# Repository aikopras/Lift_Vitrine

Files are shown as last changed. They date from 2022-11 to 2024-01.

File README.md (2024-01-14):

## Decoders and software for a model train lift (elevator, fiddle yard) ##

This software allows you to control a model train lift (elevator, fiddle yard). The photo below shows the lift at the right, and the display case (vitrine) at the left; if you click on the photo you'll see the lift in action (YouTube video; you may find there  [additional videos](https://youtube.com/playlist?list=PLT8t59Iv1uii5TKU-r4GmLXoBTifbTNtb)).

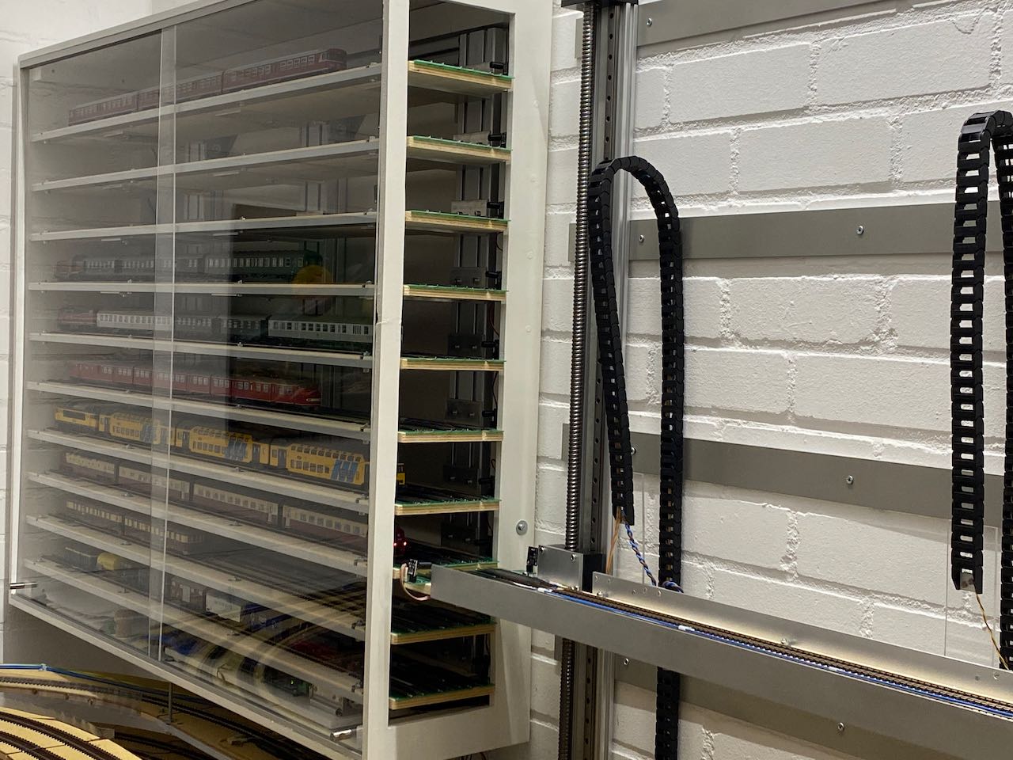
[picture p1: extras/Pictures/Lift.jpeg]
[](https://youtu.be/MswR5I-5q1c?si=-zvIIBghLZpLA2uD)

## Features ##
- Full open source (software as well as hardware).
- Can be used for up to 11 lift levels.
- The lift can be manually operated, using buttons, or by sending DCC accessory (switch) commands.
- [Full automatic operation possible](https://youtu.be/yOJ_Ovc0gCI?si=8jlIXjwKSL-hw6U0), by model train control software such as TrainController.
- Runs on ATMega 2560 processor.
- Two (open source) PCBs are available: a [SMD](https://oshwlab.com/aikopras/support-lift-controller) and a [THT](https://oshwlab.com/aikopras/lift-decoder-arduino-mega-tht) board.
- Provides feedback regarding the current lift position, as well as other status information (lift is moving, status IR-sensors)
- Feedback is provided via the (Lenz) RS-Bus. Interfacing with other feedback systems is possible, however.
- For extra safety: can be combined with IR-Sensors, to avoid lift movement if trains block the passage to/from the lift.
- For extra safety: relays can be connected to switch track power off if the lift is moving.
- Can control one or two stepper motors.
- Relies on GRBL to control the steppers motor, via a dedicated ATMega 328 / Arduino Nano.
- Allows homing, to guarantee exact positioning of the lift.
- For debugging purposes, a serial interface and / or LCD display can be connected.

## Overall structure ##
The system consists of three parts:
- **Main controller**: The main controller interfaces via the GRBL controller to the stepper drivers and motors that move the lift. The Main controller listens to DCC accessory as well as button controller commands that tell the lift to move to a certain position. The Main controller provides feedback information via the RS-Bus and its onboard connectors.
- **Button controller**: The Button controller connects to the buttons that allow manual movement of the lift. Buttons may include LEDs for visual feedback.
- **IR controller**: The IR-Sensor controller connects to the IR-LEDs and sensors that monitor if the passage to/from the lift is occupied by some train, or free.
- **RS-485**: The three controllers are connected to each other via the RS-485 bus.

A minimum system consists of a main controller only; in that case DCC switch commands will move the lift. If the button controller is attached as well, the lift may also be operated via the button interface. Note that, in such case, the lift can also be used without a DCC connection. Protection via the IR-Sensor controller enhances safety, but is optional.

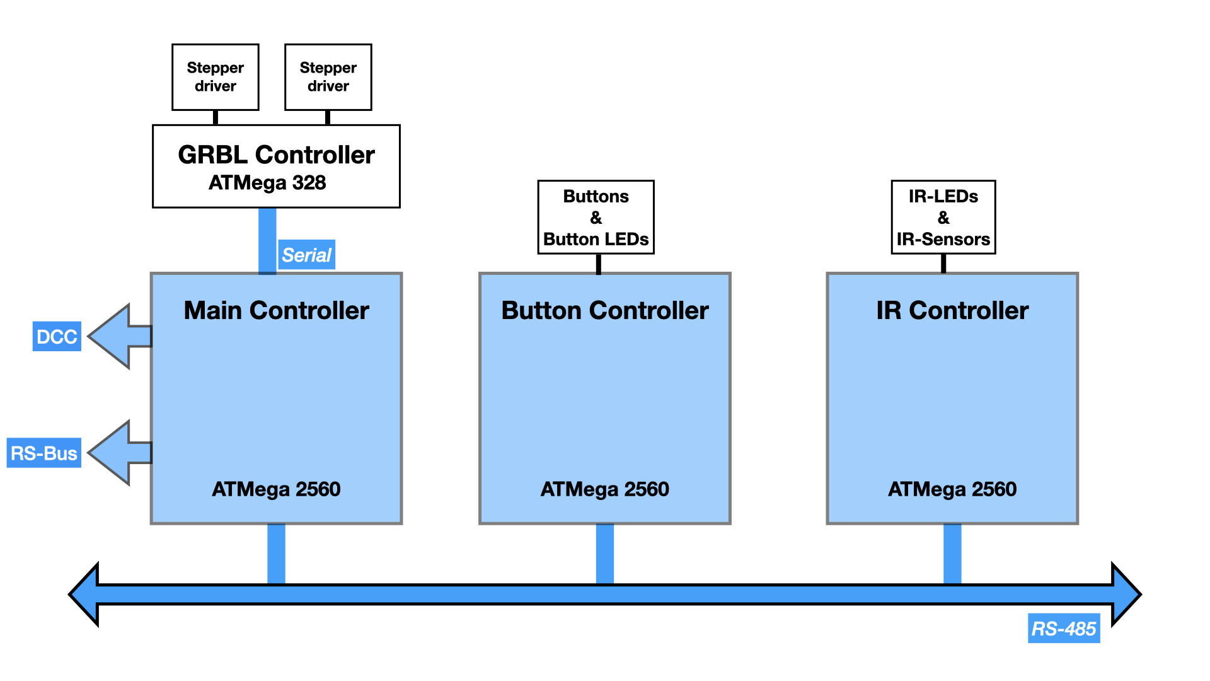
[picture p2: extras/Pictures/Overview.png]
Overview

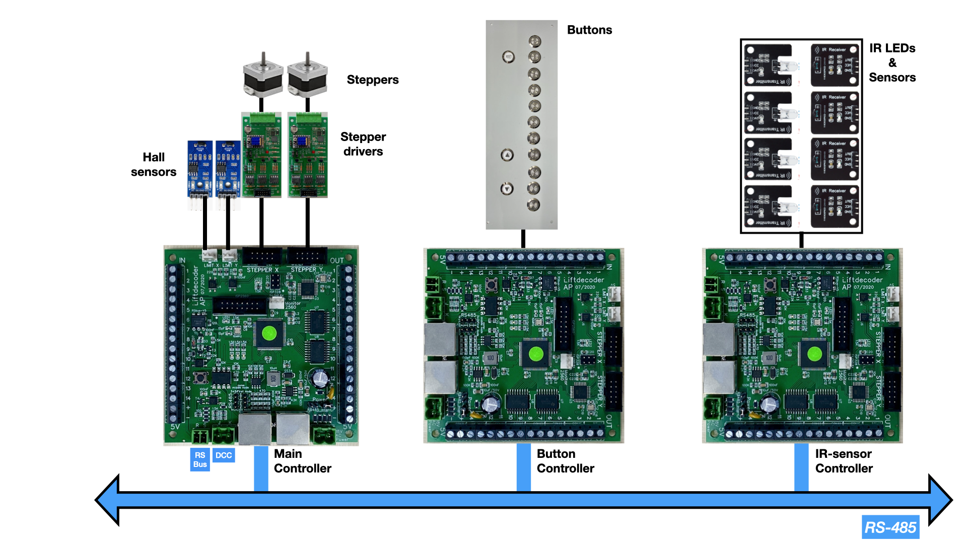
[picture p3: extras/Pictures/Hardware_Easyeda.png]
Hardware-EasyEda


## Hardware ##
Although the software runs on [standard Arduino boards](extras/Board-THT/Manual-Wiring.md), two boards were developed to make building and installation easier. Both boards are available as open source, and may be modified if desired.

#### THT Board ####
Since the software runs on standard Arduino boards, [a board that interconnects](https://oshwlab.com/aikopras/lift-decoder-arduino-mega-tht) the Arduino MEGA and NANO was developed. The board  includes a 5V power and RS485 module, which can both be bought from various (often Chinese) suppliers. The various components are all Through Hole Technology (THT), which are easy to solder. The red PCB at the bottom left side, is the RS-Bus interface, which is also open source board and available in [THT](https://oshwlab.com/aikopras/rs-bus-tht) and [SMD](https://oshwlab.com/aikopras/rs-bus-smd) versions.

The are [detailed instructions](extras/Board-THT/Assembly_Test.md) on how to compile and test software for this board.

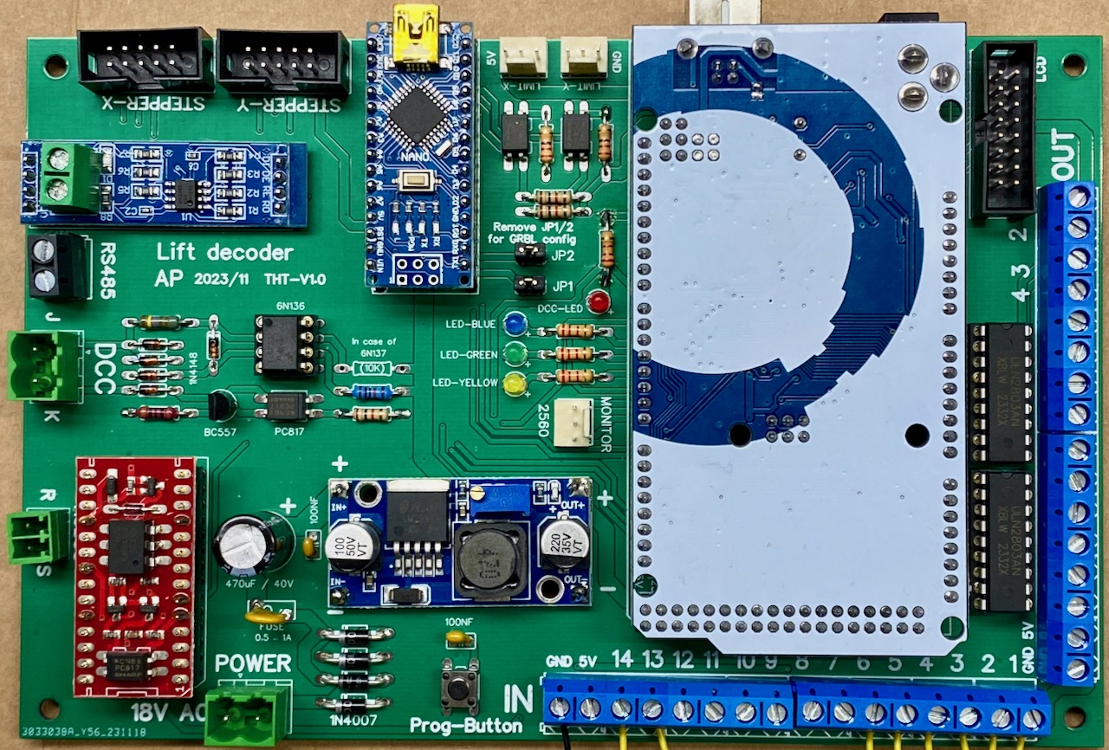
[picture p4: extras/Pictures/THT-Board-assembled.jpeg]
THT Board


#### SMD Board ####
In addition to the THT board, an open source [fully assembled SMD board](https://oshwlab.com/aikopras/support-lift-controller) was developed, that makes building even easier. In fact this board was developed first, after I discovered how cheap it was to order assembled boards in China. For five of these boards I paid in 2019 75 Euro in total. Unfortunately, component prices went up recently and now, January 2024, the costs for these five boards would be something between 125 and 150 Euro. Especially the 2560 processor has become, with 12$, quite expensive.

In September 2023 I noticed that the MP1584 Step-Down Converter is no longer *recommended for new designs*, and should be replaced by another component. That would be relatively simple change, however; on my newer boards I'm already using the TPS54331DR.

An alternative for a future board might be to replace the ATMega 2560 with one of the newer Microchip AVRs, such as an DxCore processor. In my new designs I'm using AVR32DA48 processors, which costs around 2,5$. Unfortunately replacing the chip would require, next to the board, also a redesign of some parts of the software.

The are [detailed instructions](extras/Board-SMD/Assembly_Test.md) on how to compile and test software for this board.

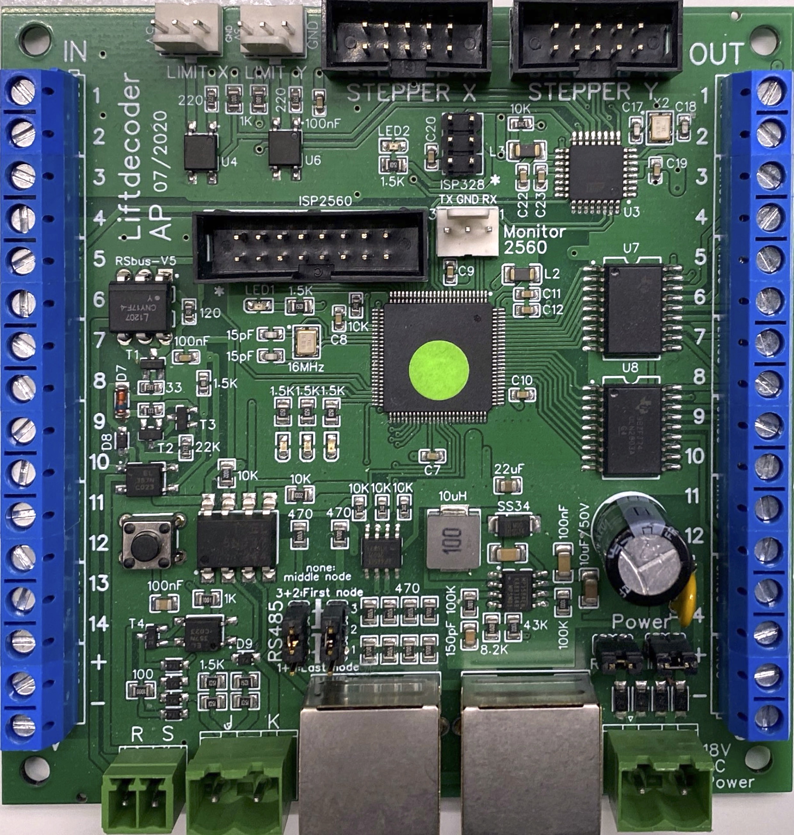
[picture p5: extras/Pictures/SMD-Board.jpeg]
SMD Board


___

## References ##
- [Detailed instructions](extras/Board-THT/Assembly_Test.md) for compiling and testing software for the THT board
- [Detailed instructions](extras/Board-SMD/Assembly_Test.md) for compiling and testing software for the SMD board
- [Loklift controller videos](https://youtube.com/playlist?list=PLT8t59Iv1uii5TKU-r4GmLXoBTifbTNtb)
- [RS485 library for the Loklift decoders](https://github.com/aikopras/AP_RS485_for_Lift_decoders)
- [Discussion of the Loklift on Beneluxspoor forum (Dutch)](https://forum.beneluxspoor.net/index.php?topic=97091.0)
- [Discussion of the Loklift on Stummiforum (German)](https://www.stummiforum.de/t203419f15-Loklift-im-Eigenbau.html)
- [PCB for the THT board](https://oshwlab.com/aikopras/lift-decoder-arduino-mega-tht)
- [PCB for the SMD board](https://oshwlab.com/aikopras/support-lift-controller)
- [PCB for stepper drivers](https://oshwlab.com/aikopras/tmc2209-driver-board)
- [PCB for the DCC/RSbus shield](https://oshwlab.com/aikopras/arduino-uno-dcc-shield)
- [PCB for the RS-Bus (THT)](https://oshwlab.com/aikopras/rs-bus-tht)
- [PCB for the RS-Bus (SMD)](https://oshwlab.com/aikopras/rs-bus-smd)
- [PCB for the RSBus feedback decoders within the vitrine (show case)](https://oshwlab.com/aikopras/vitrine-decoder)
- [PCB to connect/align the three parallel tracks in the vitrine (show case)](https://oshwlab.com/aikopras/tracks-vitrine)

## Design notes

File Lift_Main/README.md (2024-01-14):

# Main Lift Controller #

This is the software for the Main Lift Controller.
The software has been tested on the following lift decoder boards:
  - SMD board: https://oshwlab.com/aikopras/support-lift-controller
  - THT board: https://oshwlab.com/aikopras/lift-decoder-arduino-mega-tht

Instructions for compiling can be found on:
  - SMD board: https://github.com/aikopras/Lift_Vitrine/blob/main/extras/Board-SMD/Compile.md
  - THT board: https://github.com/aikopras/Lift_Vitrine/blob/main/extras/Board-THT/Compile.md

## Modes of operation ##
The Main Lift Controller can be manually and/or automatically operated:
- Manually, via pushing a button that is attached to the button controller.
- Automatically, by sending a DCC Accessory (switch) Command.

### LEDs ###
The LEDs have the following meaning:
- Blue: The blue LED blinks whenever the stepper motors are active.
- Green: The green LED indicates that power is connected and the IR sensors are free (or disabled).
- Yellow: The yellow LED mimics the LEDs on the remote button panel (without flashing).
- Red: The red LED blinks twice during startup, and once whenever a RSbus feedback message is send (see the feedback section below). If no DCC address has been connected yet, the red LED blinks continuously.

### Buttons ###
If the lift is not moving, the following button behavior is possible:
 - Short press of one of the level (0..11) buttons: Lift starts moving to the requested level.
 - Short press of the RESET button: a homing cycle will be initiated.
 - Press of ^ or v buttons: Lift moves in small steps up or down (jogging).
 - Long press of one of the level buttons: the current position will be stored as new the position for that level

While the lift moves, the associated button LED will slowly flash.
Once the move is complete, the button LED will shortly light and subsequently dim. If a new position is being stored, the button LED will flash quickly.

If the lift is moving, all buttons are ignored, except the RESET button. If the RESET button is pushed (short press), the lift will immediately be stopped (see emergence stop below).

### DCC address ###
The common approach for all my DCC decoder boards, is to compile the DCC address with an "illegal" value. This triggers the board to notify the user, via blinking of the red LED, that a DCC address needs to be entered. Like all other decoder boards, this DCC address can be set using the onboard programming button. This new address is permanently stored (in EEPROM), and the next time the decoder starts, the valid DCC address is read from EEPROM and the red LED no longer blinks.

However, you might prefer to set the DCC address already at compile time. This can be done by changing the CV1 and CV9 settings in the file [mySettings.h](mySettings.h)

### RS-Bus address ###
The onboard programming button is not only used to set the DCC address, but indirectly also the RS-Bus address. If you select a decoder address < 128 (thus a switch addresses <509), the RS-Bus address becomes equal to the decoder address (+1). If you select a decoder address >=128, the RS-Bus address becomes 0, meaning "not used". Via the onboard programming button it is therefore not possible to use decoder addresses >=128, in combination with RS-Bus feedback.

Fortunately, we can still use DCC decoder addresses >=128, in combination with RS-Bus feedback, provided we select the RSBus addresses, before compilation, in the file [mySettings.h](mySettings.h).

### Feedback ###
Feedback is provided regarding the lift's position and status. There are twelve level and three status bits. During movement of the lift, all feedback bits are cleared. The three status bits indicate if:
- the IR-sensors are free (provided IR-sensors are active)
- the Lift has arrived / is at level x. There is no movement and the stepper motors are idle
- the lift is ready.<BR>
If the IR-Sensors are active, this bit is the same as 'IR-sensors are free' AND 'Lift is at level x'.<BR>
If the IR-Sensors are inactive, this bit is the same as 'Lift is at level x'.
Analyzing this single bit may, in TrainControl (or whatever software you have), be easier than analyzing two bits.

Feedback is provided in two ways.
1. Using the RS-Bus. We use two addresses; the meaning of the individual bits, is as follows:
 - Base address    : Level 0..7                (low and high nibble. Bit 0..7)
 - Base address + 1: Level 8..11               (low nibble.          Bit 0..3)
 - Base address + 1: IR-sensors are free       (high nibble          Bit 4)
 - Base address + 1: Lift is at level x        (high nibble          Bit 5)
 - Base address + 1: Lift Ready                (high nibble          Bit 7)
2. Using the connectors on the Main Lift Board connectors (added in V2.0).<BR>
Its purpose is to facilitate the use of alternative feedback systems. Although not tested, it is expected to work with other feedback interfaces, such as the LDT RM-88-N-O, the YaMoRC YD6016LN-OPTO and YD6016ES-OPTO, Uhlenbrock 63330 etc.

  - The connectors labelled "IN 1..12" are used to tell which level the lift currently is.
  The connector labelled "1" is for level "0", etc.
  - The connector labelled "IN 13" is used to tell that IR-sensors are free.
  - The connector labelled "IN 14" is used to tell that lift has arrived / is  at level x.
  - The pin labelled "OUT 1" is to tell that the lift is ready.

Note that the IN connectors are directly connected to pins on the ATMega 2560 processor, (accidental) shortcut of these pins will destroy the processor.
Therefore ensure you always use resistors with a value of 1 kOhm or higher.

### Emergency stop ###
If the lift is moving, it can be stopped by either pushing the RESET button, or by sending a DCC Emergency Stop command (= Broadcast ResetCmd). In both cases the RESET button will quickly flash.
1. BUTTON: The Button generates a soft_reset, which immediately halts the steppers and resets GRBL. If reset while in motion, GRBL will throw an Alarm to indicate position may be lost from the motion halt. The Alarm state is signaled via the RESET Button LED, which quickly flashes. A second push of the RESET button is needed to leave the Alarm state. The lift stays at an  undefined position.
2. DCC Emergency Stop command: generates a GRBL feedhold, This allows to lift to continue its movement afterwards. In case the lift should not restart its movement after the DCC emergency stop, while still in the HOLD state, the reset-button which will trigger a soft-reset.

# Initialization #
Before the Main Lift Controller can be used, a number of settings must first be made in the file [mySettings.h](mySettings.h).

##### 1) Tell the sketch which board will be used #####
As mentioned at the top of this page, the lift controller code has been tested on a SMD and a THT board. Although the decoder software will also run on other boards, it is important that the processor is an ATMega 2560 and that the correct connections are made between the processor pins and the various peripherals. Some of these assignments are made in the file [hardware.h](hardware.h) (the DCC, RSBus and RS485 assignments are made by their respective libraries). As can be seen in that file, some small differences exists between the pin assignments for both boards. The reason behind these differences, is that the SMD board  was developed first, and some pins were used that are not available on standard Arduino MEGA boards. Later the THT board was developed, which made some pin changes necessary. The choice between both boards is made via a `#define`.

To use the SMD board, enable the associated `#define`.
```
    #define BOARD_SMD
```
For the THT board, enable the other `#define`:
```
    #define BOARD_THT
```
##### 2) Homing #####
By default, a homing cycle for the stepper motor(s) is performed at program start. Such homing cycle ensures that the lift will move to a defined position. Uncomment the `#define` (remove the starting //) if homing is NOT desired.
```
    #define NO_HOMING
```

##### 3) IR-Sensors #####
By default, every time before the lift starts moving, the IR-sensors connected to the dedicated IR-Sensor Board will be checked. If a train blocks an IR-beam, the lift will not move. Uncomment the `#define` if the IR-sensors should not be checked. This may be required for testing purposes, or if no IR_Sensor board is connected and needed.
```
    #define NO_IR_SENSORS
```

##### 4) LCD Display #####
By default, the LCD is disabled, to avoid interference with RS-bus feedback and other time critical functions. Such interference is caused by the fact that writing to the LCD screen takes quite some time. For testing purposes, or in cases where time critical functions like RS-bus feedback are not needed, the LCD display may be enabled.
```
    #define ENABLE_LCD
```

##### 5) SERIAL_MONITOR #####
By default, the serial monitor interface is switched off (value = 0).
For entering GRBL commands or debugging, it may be convenient to enable the serial monitor.<BR>
If the value = 1, input from the serial line will be copied to the GRBL processor, and information gets displayed regarding the current lift position.<BR>
If the value = 2, input from the serial line will be copied to the GRBL processor, and all data coming back from the GRBL processor gets displayed.
```
    #define SERIAL_MONITOR 1
```

##### 6) DCC Address #####
The decoder can listen to DCC accessory commands to move the lift to a certain level. Each lift level has its own switch address; the first switch address is for level 0; the second switch address is for level 1, the third for level 2, etc.<BR>
Per 4 switch addresses we need one decoder address. Since the maximum number of lift levels is 12, we listen to three decoder addresses.

The first decoder address is stored in CV1 plus CV9. The relationship between CV1, CV9  and the decoder address is explained in RCN-213 (Section 2.1) and RCN-225.
- the valid range for CV1 is 1..63 (if CV9 == 0) or 0..63 (if CV9 !=0)
- the valid range for CV9 is 0..3  (or 128, if the decoder has not been initialized).

If you don't `#define` these CVs here, the default value for CV1 (myAddrL) = 1 and for CV9 (myAddrH) = 128 (0x80). A CV9 value of 128 indicates that the address has not been set by the user yet (by pushing the button).
In that case the decoder's red LED starts blinking.

If your lift will not  be controlled by DCC, but only manually by buttons, you should change CV9 to 0.

Uncomment both `#defines` below and fill-in the address CVs yourself
```
    #define CV1 56
    #define CV9 3
```

##### 7) Set the RS-Bus addresses #####
The RS-Bus address is stored in CV10 (myRSAddr). Valid addresses are between 1..128. The default value is 0, meaning that the RSbus becomes inactive.
The RS-Bus address 128 is used by all my decoders for PoM feedback.
We need two RS-Bus addresses for all feedback information; only the first address needs to be entered below. This address should therefore be between 1..126.
```
    #define RS_ADDRESS 126
```

#### 8) Relays ####
The decoder board allows the connection of two (bi-stable) relays. These relays can, for example, be used to:
1. ensure that the track that connects the lift to the remaining tracks, will only be powered whenever the lift is at level 0. This would be an additional safety measure
2. allow a change of boosters, depending if the lift is at level 0 or at another level. This avoids potential problems at the border between two booster sections

In case the lift is IDLE and at level 0, both relays will be switched to "position 1". In all other cases both relays will be switched to "position 2".

You may change the pins for external relays, provided they stay somewhere on the OUT 9..14 pins (Port K). If you don't use any relays, just keep the values below.
```
    #define RELAY1_POS1    63  // PIN_PK1 - Number on PCB: OUT 10
    #define RELAY1_POS2    64  // PIN_PK2 - Number on PCB: OUT 11
    #define RELAY2_POS1    65  // PIN_PK3 - Number on PCB: OUT 12
    #define RELAY2_POS2    66  // PIN_PK4 - Number on PCB: OUT 13
```

*Note:* The Lift-decoder outputs become, once activated, low. The load should therefore be connected between the output and +5V. Once activated, the differential voltage becomes something like 4 Volt. This might be enough for a 5 (or 3,3V) relay, but certainly not for a 12V relay. Therefore the connection towards 12V relays should be performed via optocouplers, which "translate" between the 5V output domain, and a separate 12V domain for the relays.   

#### 9) Initial lift positions ####
Initial lift positions. Will be entered into EEPROM if and only if the EEPROM has not been initialized. Once the EEPROM is initialized, values will not be written to EEPROM again, even if you make changes in [mySettings.h](mySettings.h). Later changes regarding lift positions should be made via the buttons.

In case you don't have buttons (since the lift is operated via DCC only), you can enable FORCE_EEPROM_WRITE (see below).
After these values are stored in EEPROM, do NOT modify the values again!! Values are in millimeter (point as decimal separator).
```
    #define LEVEL00       "0.000"
    #define LEVEL01     "100.000"
    #define LEVEL02     "200.000"
    #define LEVEL03     "300.000"
    #define LEVEL04     "400.000"
    #define LEVEL05     "500.000"
    #define LEVEL06     "600.000"
    #define LEVEL07     "700.000"
    #define LEVEL08     "800.000"
    #define LEVEL09     "900.000"
    #define LEVEL10    "1000.000"
    #define LEVEL11    "1100.000"
```

#### 10) Force EEPROM write ####
Set the `#define` below to `1`, if the new values MUST be written to EEPROM. Don't forget to change it back to `0` once the new settings are stored in EEPROM, to avoid EEPROM wear-out.
```
    #define FORCE_EEPROM_WRITE 0
```

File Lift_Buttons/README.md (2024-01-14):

# Buttons controller #

This is the software for the Buttons controller.
The software has been tested on the following lift decoder boards:
  - SMD board: https://oshwlab.com/aikopras/support-lift-controller
  - THT board: https://oshwlab.com/aikopras/lift-decoder-arduino-mega-tht

Instructions for compiling can be found on:
  - SMD board: https://github.com/aikopras/Lift_Vitrine/blob/main/extras/Board-SMD/Compile.md
  - THT board: https://github.com/aikopras/Lift_Vitrine/blob/main/extras/Board-THT/Compile.md

### LEDs ###
**Blue LED:** The blue LED blinks whenever a RS485 request message is received from the main Lift decoder. The main Lift controller polls the Buttons controller every 100ms if a button is pushed. In normal operation the blue LED should therefore blink 10 times per second.

**Green LED:** The green LED indicates the board is powered and the sketch is started.

**Yellow LED:** The yellow LED is set immediately after a button is pushed. It stays on, until an explicit command is received from the Main Lift Controller, saying that the action associated with the button is completed.

**Red LED:** The red LED is not used by the Buttons Controller software.

### Wiring ###
The board has 14 inputs (`IN 1..14`) and 14 outputs (`OUT 1..14`). The outputs are used for the LEDs that are build into each and every button.
The buttons for the various levels should be wired to the `IN 1..11`pins; the Reset button to `IN 12`, and the UP and DOWN buttons to `IN 12` resp. `IN 13`. The other side of the buttons should be connected to `GND`. The LEDs, however, should be connected between the `OUT` pins and` +5V`.

In case you want to make changes, the meaning of the various pins is not defined in the button controller sketch, but in  [rs485.h](../Lift_Main/rs485.h) of the main controller sketch.
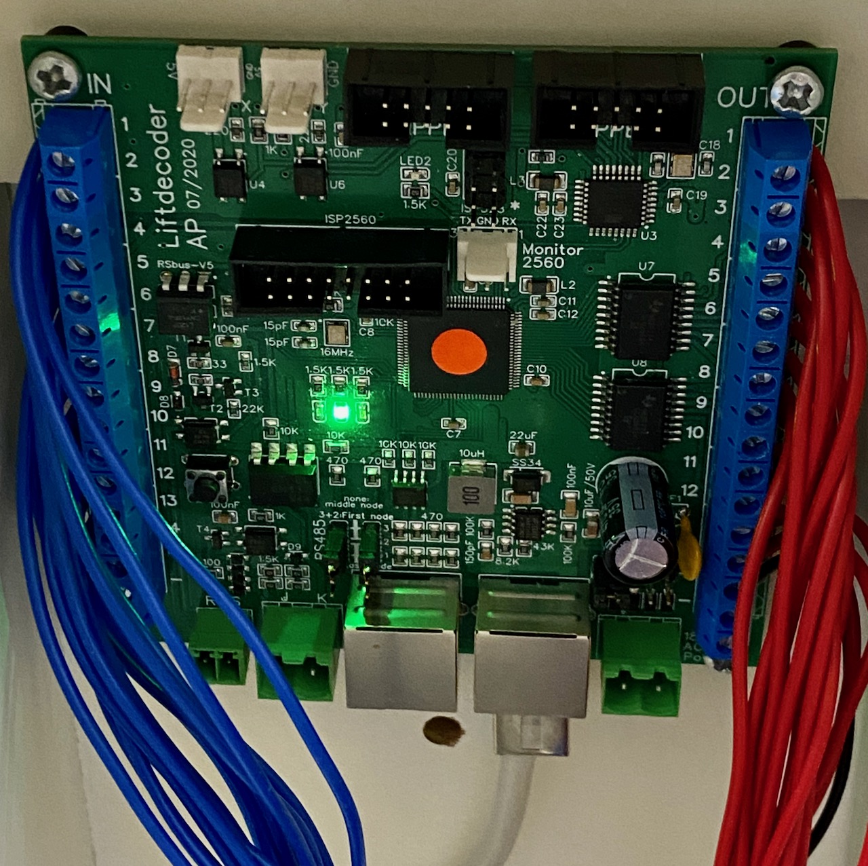
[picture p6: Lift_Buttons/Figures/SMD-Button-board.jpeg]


## Initialization ##
Before the Buttons-controller can be used, the following setting must be made first in the file [mySettings.h](mySettings.h).

##### 1) Tell the sketch which board will be used #####
As mentioned at the top of this page, the lift controller code has been tested on a SMD and a THT board. Although the decoder software will also run on other boards, it is important that the processor is an ATMega 2560 and that the correct connections are made between the processor pins and the various peripherals. Some of these assignments are made in the file [hardware.h](hardware.h) (the DCC, RSBus and RS485 assignments are made by their respective libraries). As can be seen in that file, some small differences exists between the pin assignments for both boards. The reason behind these differences, is that the SMD board  was developed first, and some pins were used that are not available on standard Arduino MEGA boards. Later the THT board was developed, which made some pin changes necessary. The choice between both boards is made via a `#define`.

To use the SMD board, enable the associated `#define`.
```
    #define BOARD_SMD
```
For the THT board, enable the other `#define`:
```
    #define BOARD_THT
```

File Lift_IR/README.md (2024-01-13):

# IR-sensor controller #

This is the software for the Infra-Red (IR) sensor controller.
The software has been tested on the following lift decoder boards:
  - SMD board: https://oshwlab.com/aikopras/support-lift-controller
  - THT board: https://oshwlab.com/aikopras/lift-decoder-arduino-mega-tht

Instructions for compiling can be found on:
  - SMD board: https://github.com/aikopras/Lift_Vitrine/blob/main/extras/Board-SMD/Compile.md
  - THT board: https://github.com/aikopras/Lift_Vitrine/blob/main/extras/Board-THT/Compile.md

### LEDs ###
**Blue LED:** The blue LED blinks whenever a RS485 request message is received from the main Lift decoder. The main Lift controller polls the IR-controller every 100ms for the status of all IR sensors. In normal operation the blue LED should therefore blink 10 times per second.

**Green LED:** The green LED is on, as long as all IR-Sensors are free. At the moment a train blocks an IR-beam, the LED turns off. The IR-sensors are checked 10 times per second, thus changes will be detected within 100ms.

**Yellow LED:** In normal operations the yellow LED will be off. However, by pushing the onboard button, the decoder may be put in debugging mode (see below).

**Red LED:** The red LED blinks twice during startup, and once whenever a RSbus feedback message is send. Such feedback messages are send whenever a change in the status of one or more sensors is detected.

### Debugging mode ###
Debugging mode is entered, whenever the onboard button is pushed. If the button is pushed again, debugging mode will be turned off. The yellow LED indicates whether debugging mode is on or off.

In debugging mode, status information of every individual sensor is send over the Serial Interface and can thus be examined using the Arduino's Serial Monitor. Baudrate should be 115200 baud.

Sending data over the Serial Line is relatively CPU intensive and may sometimes interfere with normal operations. Therefore debugging mode should be off, unless you really need to check for errors.
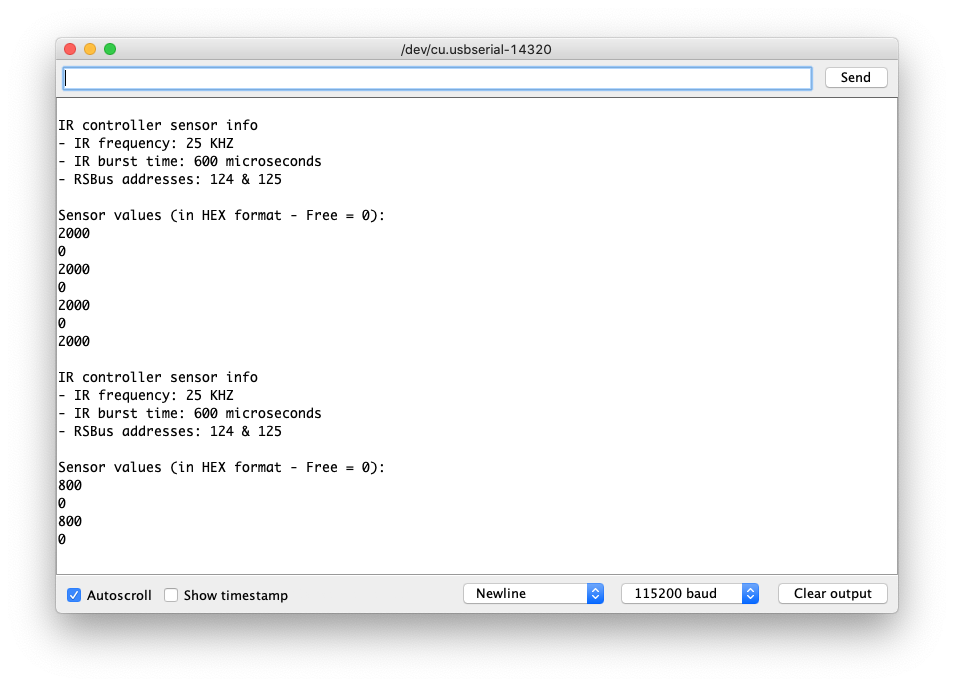
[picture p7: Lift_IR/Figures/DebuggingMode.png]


## Sensors ##
For my lift, I've used the following IR-LEDs and Sensors. They are quite inexpensive and can be obtained from sources such as Ali. A problem with these LEDs, is that light goes into many directions, potentially leading to reflections. Due to reflections, the sensor (receiver) may still receive IR-light, despite the fact that the direct beam is blocked by a train. Therefore, to focus the IR-beam a bit, a black tube has been put around the sides of the LED.

##### Connections: #####
  - Receiver: GND goes to the decoder's GND (-), VCC goes to the decoder's 5V; DAT goes to one of the 14 decoder's input pins.
  - IR-LED: S (pin left) goes via a resistor of 1 Kohm or higher to the decoder's 5V; - (pin right) goes to the corresponding decoder's output pin; the pin in the middle will not be connected. Note that the LED *must* be connected (via a resistor) between the output pin and ***+5V***, and not to the decoder's *GND (-)*. This is because the decoder uses ULN 2803 output drivers, which are either Low or Undefined.

<table><tr>
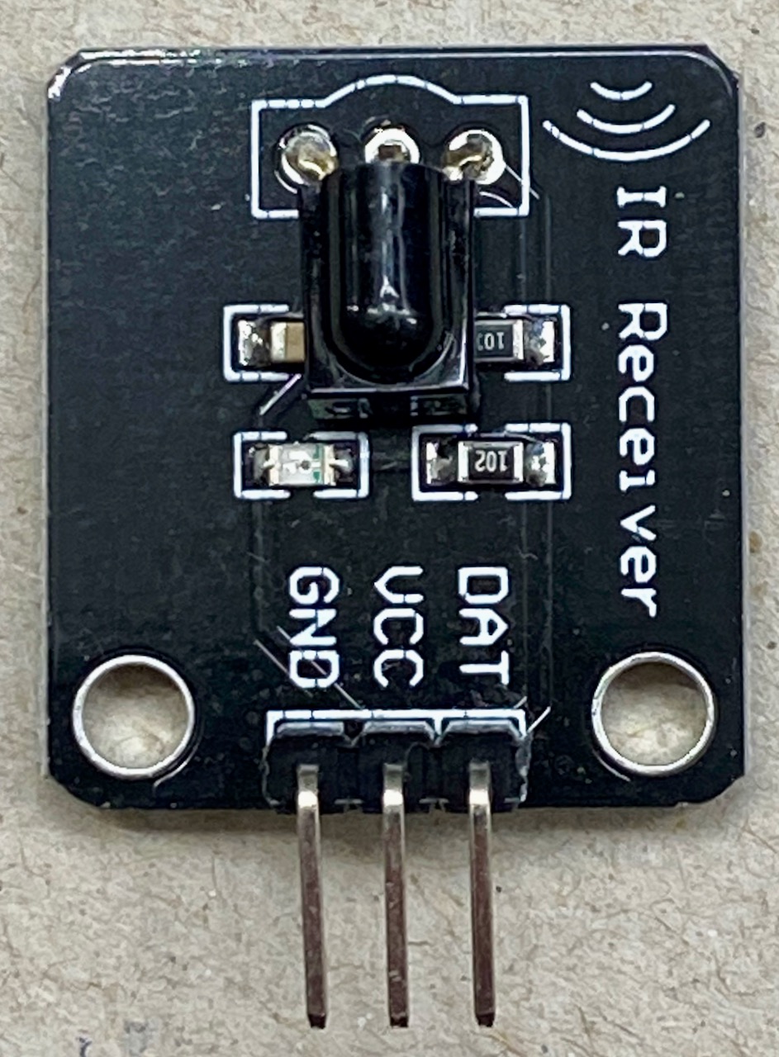
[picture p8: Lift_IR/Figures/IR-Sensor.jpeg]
Sensor
<td>  </td>
<td> <img src="Figures/IR-LED2.jpeg" alt="IR-LED2" "/> </td>
</tr></table>

## Initialization ##
Before the IR-controller can be used, a number of settings must be made first in the file [mySettings.h](mySettings.h).

##### 1) Tell the sketch which board will be used #####
As mentioned at the top of this page, the lift controller code has been tested on a SMD and a THT board. Although the decoder software will also run on other boards, it is important that the processor is an ATMega 2560 and that the correct connections are made between the processor pins and the various peripherals. Some of these assignments are made in the file [hardware.h](hardware.h) (the DCC, RSBus and RS485 assignments are made by their respective libraries). As can be seen in that file, some small differences exists between the pin assignments for both boards. The reason behind these differences, is that the SMD board  was developed first, and some pins were used that are not available on standard Arduino MEGA boards. Later the THT board was developed, which made some pin changes necessary. The choice between both boards is made via a `#define`.

To use the SMD board, enable the associated `#define`.
```
    #define BOARD_SMD
```
For the THT board, enable the other `#define`:
```
    #define BOARD_THT
```
##### 2) Tell the sketch which I/O ports are used for the sensors #####
The lift decoder boards have 14 general purpose in- and outputs. Therefore a maximum of 14 sensors (IR-LEDs and IR-Receivers) may be connected (the software would facilitate 16). To tell the software which inputs/outputs are wired, a bitmask `MASK_SENSORS_CONNECTED` is used. The lowest order (rightmost) bit in that mask corresponds to the IN/OUT pair of the blue connectors that are labelled 1. Below are some examples:
 - `0b0000000000000001` a single sensor is connected to IN/OUT 1
 - `0b0000000000000011` two sensors are connected to IN/OUT 1 and 2
 - `0b0000000000000010` a single sensor is connected to IN/OUT 2
 - `0b0000111111111111` twelve sensors are connected to IN/OUT 1..12
 - `0b0011111111111111` all 14 sensors are connected

Again a `#define` is used to set the bit mask. Below the default setting for twelve sensors connected to IN/OUT 1..12:
```
    #define MASK_SENSORS_CONNECTED 0b0000111111111111
```

##### 3) Set the sensor sensitivity #####
The sensitivity of the IR LEDs and receivers is best around 38kHz. Unfortunately, at 38kHz the system may become too sensitive, allowing reflections to generate false negatives. A false negative occurs whenever a train blocks the direct IR-beam between LED and receiver, but because of reflections the receiver still receives IR-signals and therefore fails to detect the train.

There are several means to limit the effect of reflections. First, the software checks a single LED-receiver pair at a time; the receiver therefore never receives a beam coming from a different LED. Second, a small tube around the LED (see photo above) will focus the beam into a smaller beam. Third, the resistor in series with the LED limits the current flowing through the LED, and thus the strength of the IR-beam. In my layout I've used resistors with a value of 1 kOhm, but in hindsight a higher value would have been a better choice.

Fortunately there are also other ways to limit sensitivity. IR-LEDs and receivers usually operate at 38kHz, but will also operate at lower (or higher) frequencies, although less sensitive. To decrease the sensitivity of the sensors, we can therefore lower the frequency to, for example, a value of 25kHz. Depending on your specific situation, you may have to experiment with this value to find the value that works best. Again we will use a `#define` for that.

Next to modifying the KHZ value, we may also play with the time the burst lasts. To avoid the receiver from saturation, the burst of IR pulses may not become too long. In practice, a reasonable value will be something between 15 to 30 pulses, which corresponds (roughly) to anything between 375 us (15 x 25) and 750 us.

Below are the default values for 25 kHz and 600 us burst time:
```
#define KHZ 25                       // Frequency at which we operate the IR system
#define BURST_TIME 600               // Time in us the burst will last
```

##### 4) Set the RS-Bus addresses #####
Although the Main Lift Controller board signals to the DCC system / control computer whether all IR-Sensors are free or not (using a single bit), it may sometimes be convenient to also know the status of each individual sensor. This is particularly true in case of possible errors.  To facilitate individual sensor feedback, we use the RS feedback bus. We need two RSBus addresses for that, to accommodate a maximum of 16 sensors (although the board supports "only" 14 sensors).

You may change the addresses to any value you like. In case you don't use RSBus feedback, you should still have the addresses configured, to avoid compile errors. Below are the default values (note that this time we do not use a `#define`, but `const uint8_t`):
```
const uint8_t RS_AddresLow = 124;     // 1.. 128
const uint8_t RS_AddresHigh = 125;    // 1.. 128
```

##### 5) Speed versus portability #####
To increase speed, we can use for the IR-beam generation two of the three General Purpose I/O Registers (GPIORs) that are available on a ATMega 2560.
```
    #define PORT GPIOR0                   // Fast, but may interfere with other libraries
    #define BITMASK GPIOR1                 
```
To use these GPIORs, we have to be certain however that they are not yet used elsewhere in the software. The AP-DCC-Library, for example, already uses GPIOR0 and GPIOR1. In cases where we know that we can't use these GPIORs, or in cases where we obtain strange errors, we can use `volatile uint8_t` variables instead. This makes the code run less efficient, but improves portability.

```
    volatile uint8_t PORT;              // Slow, but more portable
    volatile uint8_t BITMASK;
```

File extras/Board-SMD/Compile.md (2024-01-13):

## MegaCore - Compile and upload ##

To compile and upload a lift-decoder sketch, select the MegaCore board, the ATmega 2560 processor, MEGA pinout, and "no bootloader". For other settings see below. Select the programmer you have. <BR>
Upload the sketch (**Upload** button or **Sketch => Using Programmer**).
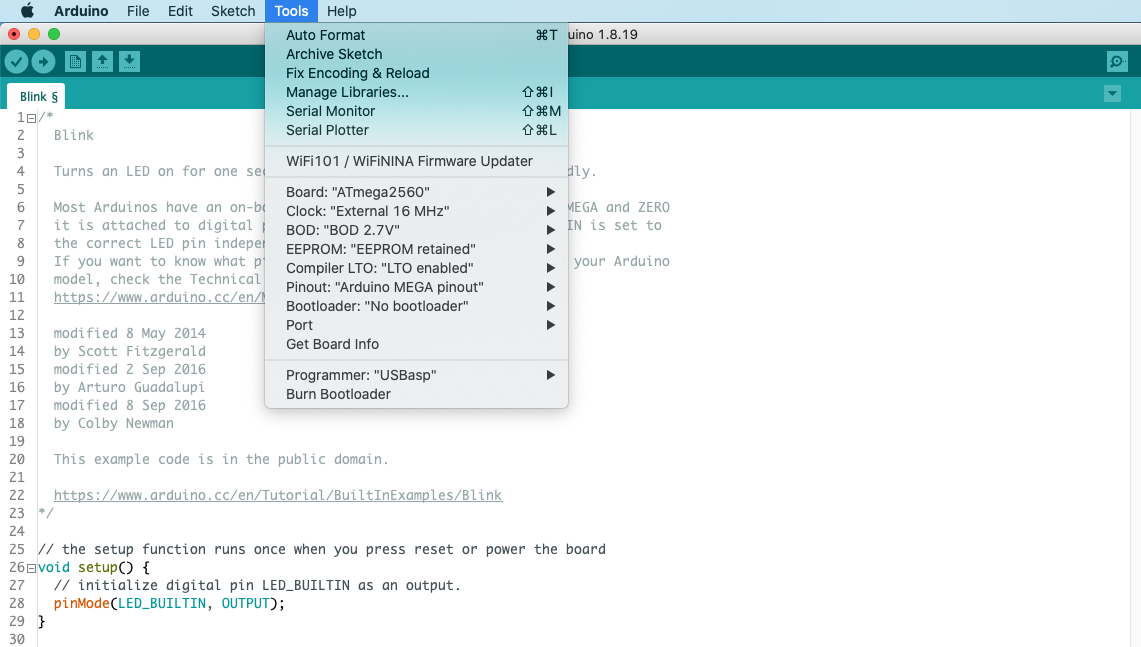
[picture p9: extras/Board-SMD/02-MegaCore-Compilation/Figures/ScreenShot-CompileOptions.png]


### MegaCore ###
If the Fuses have not yet been set or the MegaCore board  installed, see the instructions [here](./02-MegaCore-Compilation/Step02-MegaCore-Compilation.md)

### EEPROM retained? ###
The **Tools** menu includes an option called **EEPROM retained**. The idea behind this option is that, during compilation, a choice can be made whether the EEPROM should keep its current values, or be cleared / overwritten. Unfortunately, clearing / overwriting seems to be quite unreliable, and depend on several factors, including if / which bootloader is used. In practice the EEPROM will most likely *NOT* be cleared / overwritten.

The Lift decoder boards (and any board that uses the AP_DCC_Decoder_Core library) therefore check, at startup, if the EEPROM is empty (that happens if you use a new board). If that is the case, the EEPROM will be automatically filled with default values (from the [AP_DCC_Decoder_Core](https://github.com/aikopras/AP_DCC_Decoder_Core/blob/main/src/CvValues/CvValues.cpp) library).

In the setup() part of your sketch you may [override](https://github.com/aikopras/AP_DCC_Decoder_Core/blob/main/src/CvValues/CvValues.md) these initial CV values. To store these new CV values in EEPROM, you have to push the onboard button for 5 seconds (or use a PoM message and write to CV8).

The main lift decoder has, in the mySettings.h file, a compiler directive called FORCE_EEPROM_WRITE that will overwrite the EEPROM with new values. This directive can be used instead of the **EEPROM** retained" option in the **Tools** menu.

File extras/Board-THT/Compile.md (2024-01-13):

## MegaCore - Compile and upload ##

To compile and upload a lift-decoder sketch, select the MegaCore board, the ATmega 2560 processor and as Programmer the "Legacy Arduino MEGA bootloader". See below for the other settings. <BR>
Upload the sketch (**Upload** button).
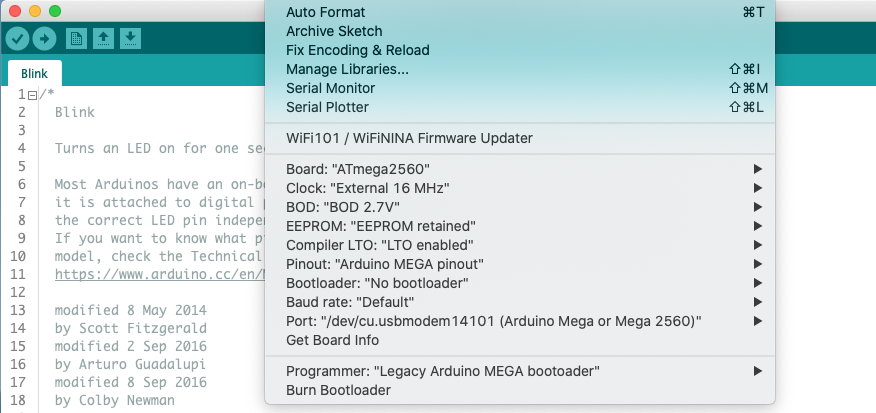
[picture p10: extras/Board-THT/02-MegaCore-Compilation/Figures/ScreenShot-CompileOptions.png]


### MegaCore ###
If the MegaCore board has not yet been installed, see the instructions [here](./02-MegaCore-Compilation/Step02-MegaCore-Compilation.md)

### EEPROM retained? ###
The **Tools** menu includes an option called **EEPROM retained**. The idea behind this option is that, during compilation, a choice can be made whether the EEPROM should keep its current values, or be cleared / overwritten. Unfortunately, clearing / overwriting seems to be quite unreliable, and depend on several factors, including if / which bootloader is used. In practice the EEPROM will most likely *NOT* be cleared / overwritten.

The Lift decoder boards (and any board that uses the AP_DCC_Decoder_Core library) therefore check, at startup, if the EEPROM is empty (that happens if you use a new board). If that is the case, the EEPROM will be automatically filled with default values (from the [AP_DCC_Decoder_Core](https://github.com/aikopras/AP_DCC_Decoder_Core/blob/main/src/CvValues/CvValues.cpp) library).

In the setup() part of your sketch you may [override](https://github.com/aikopras/AP_DCC_Decoder_Core/blob/main/src/CvValues/CvValues.md) these initial CV values. To store these new CV values in EEPROM, you have to push the onboard button for 5 seconds (or use a PoM message and write to CV8).

The main lift decoder has, in the mySettings.h file, a compiler directive called FORCE_EEPROM_WRITE that will overwrite the EEPROM with new values. This directive can be used instead of the **EEPROM** retained" option in the **Tools** menu.

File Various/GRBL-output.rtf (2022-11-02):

Below some GRBL input (in red) and the corresponding output.
A detailed description is provided at: https://github.com/gnea/grbl/wiki/Grbl-v1.1-Interface

?
<Idle|MPos:0.000,0.000,0.000|FS:0,0|Ov:100,100,100>
ok

X100
ok
?
<Run|MPos:88.028,0.000,0.000|FS:903,0>
ok
?
<Idle|MPos:100.000,0.000,0.000|FS:0,0>
ok

G90 X300
ok
?
<Run|MPos:283.913,0.000,0.000|FS:1047,0>
ok
?
<Idle|MPos:300.000,0.000,0.000|FS:0,0>
ok

XYZA
error:2

$H (maar zonder switches)
ALARM:8
ok

Grbl 1.1h ['$' for help]
[MSG:'$H'|'$X' to unlock]

$X
[MSG:Caution: Unlocked]
ok

? (Na een mislukte Homing cyclus)
<Idle|MPos:7.700,7.700,0.000|FS:0,0|WCO:0.000,0.000,0.000>
ok

G91 X250
ok
?
<Run|MPos:35.269,7.700,0.000|FS:1434,0|Ov:100,100,100>
ok
?
<Run|MPos:112.191,7.700,0.000|FS:2000,0>
ok
?
<Run|MPos:193.713,7.700,0.000|FS:2000,0>
ok
?
<Run|MPos:246.203,7.700,0.000|FS:884,0>
ok
?
<Idle|MPos:257.700,7.700,0.000|FS:0,0>
ok
?
<Idle|MPos:257.700,7.700,0.000|FS:0,0>
ok

G90 X100
ok
?
<Run|MPos:110.163,7.700,0.000|FS:831,0>
ok
?
<Idle|MPos:100.000,7.700,0.000|FS:0,0>
ok

0123456789ABCDEFGHIJK
<Idle|MPos:0.000,

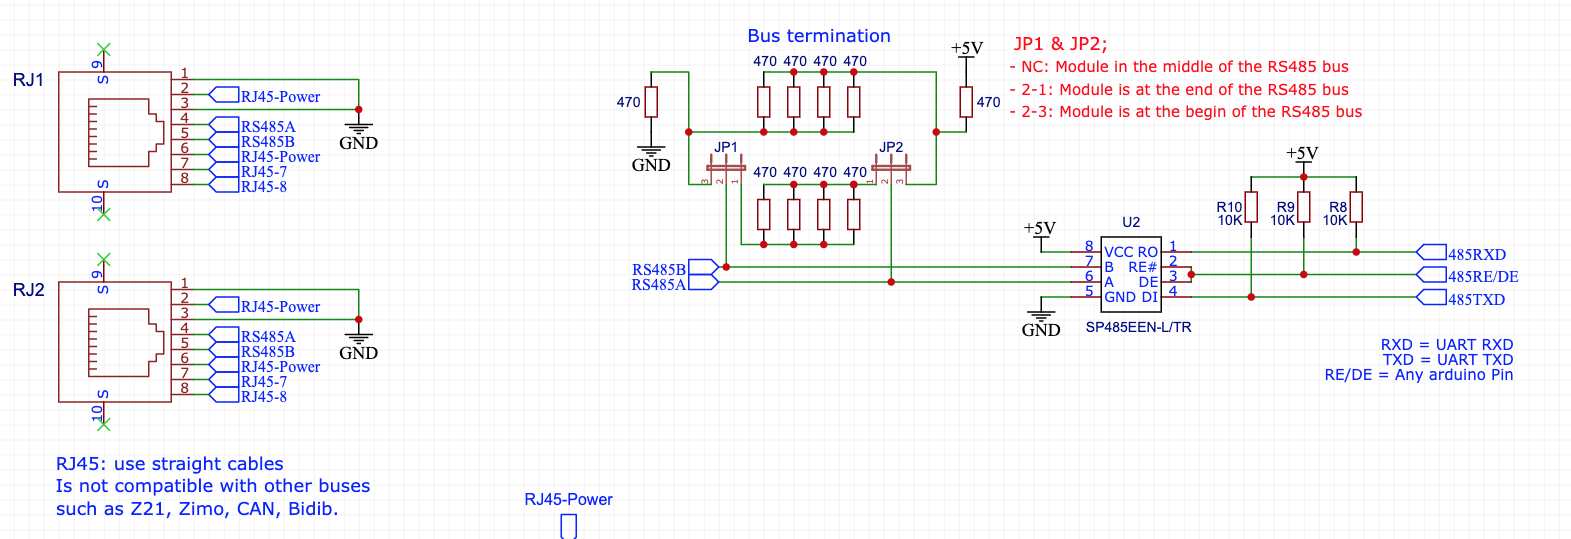
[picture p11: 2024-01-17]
extras/Board-SMD/05-RS485/Figures/RS485-Schematics.png

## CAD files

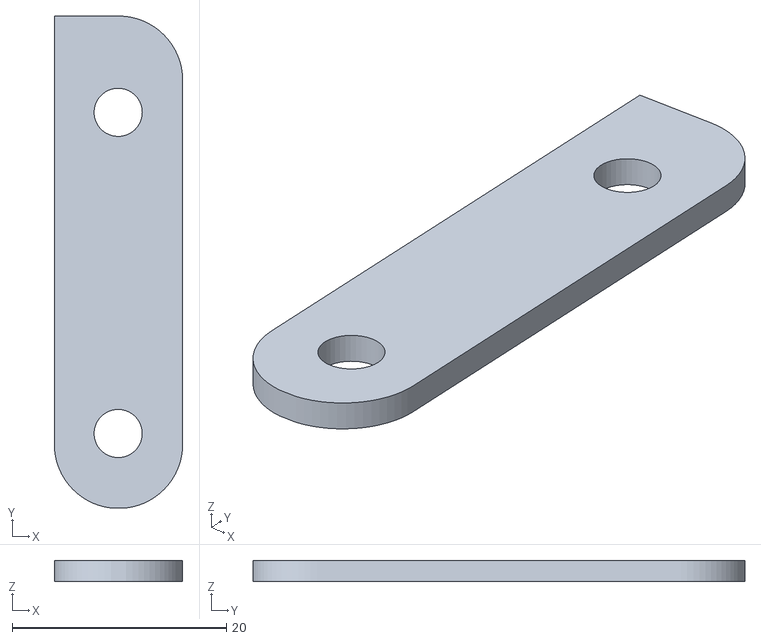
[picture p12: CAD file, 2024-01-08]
extras/Board-SMD/04-GRBL-and-steppers/3D_Hall-sensor/Magnet-2.stl
12.0 x 46.0 x 2.00

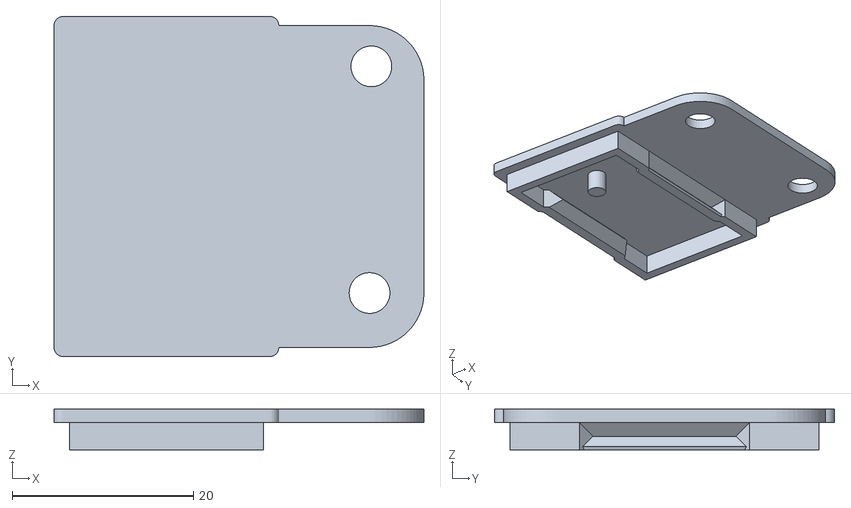
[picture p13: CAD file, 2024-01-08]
extras/Board-THT/04-GRBL-and-steppers/3D_Hall-sensor/Sensor-Part-1.stl
40.8 x 37.5 x 4.50

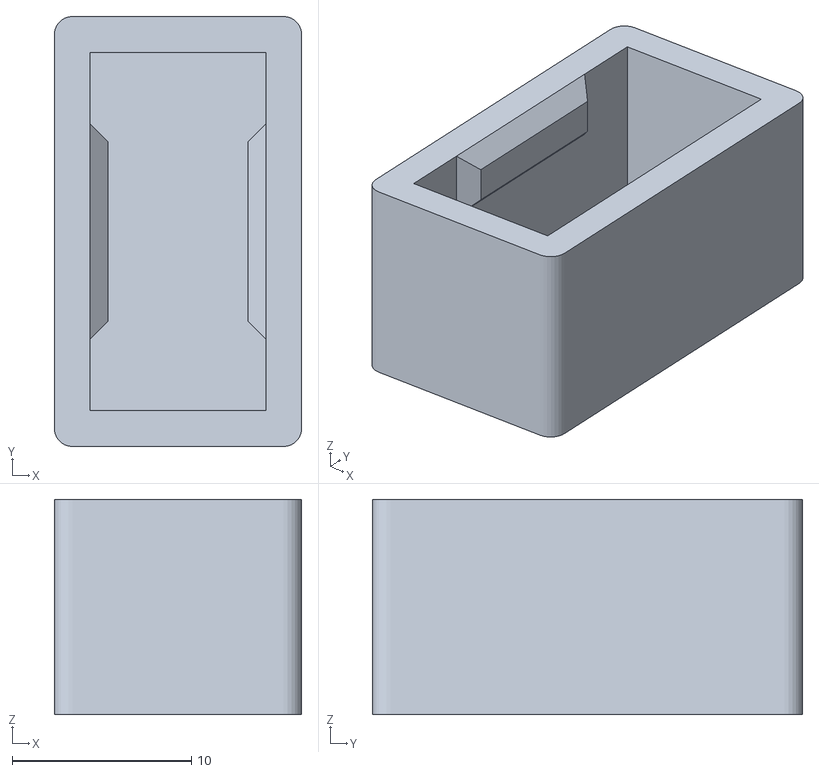
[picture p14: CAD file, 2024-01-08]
extras/Board-SMD/04-GRBL-and-steppers/3D_Hall-sensor/Magnet-3.stl
13.8 x 24.0 x 12.0

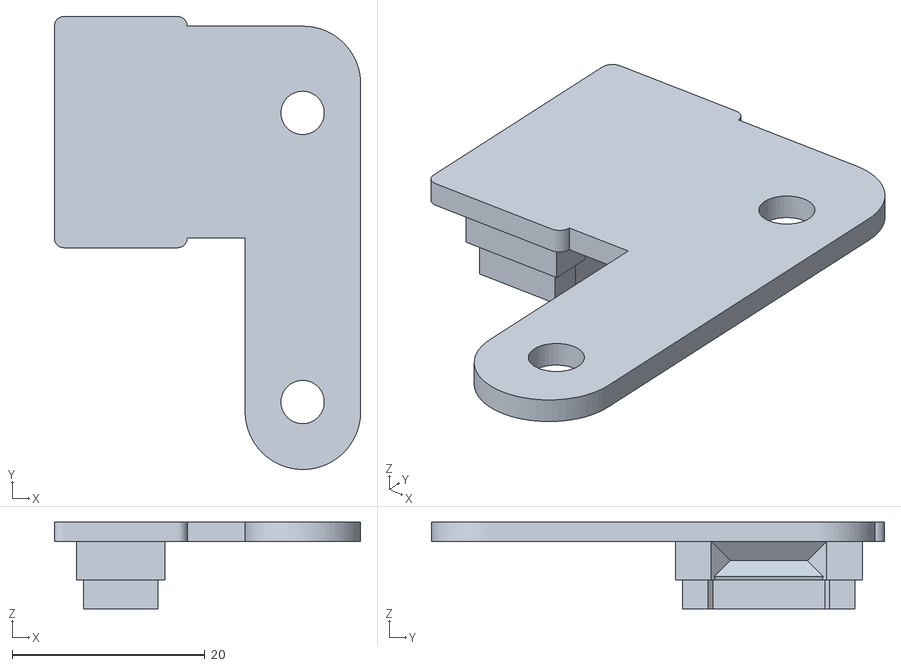
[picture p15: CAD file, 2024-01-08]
extras/Board-SMD/04-GRBL-and-steppers/3D_Hall-sensor/Magnet-1.stl
31.8 x 47.0 x 9.00

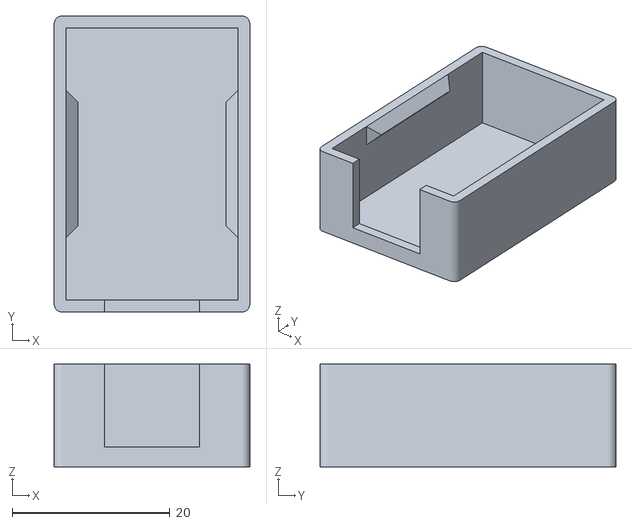
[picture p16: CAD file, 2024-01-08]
extras/Board-SMD/04-GRBL-and-steppers/3D_Hall-sensor/Sensor-Part-2.stl
24.8 x 37.5 x 13.0

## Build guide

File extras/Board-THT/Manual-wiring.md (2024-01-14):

## Manual wiring ##

Although I wouldn't recommend this, in principle it is possible to run the software on standard Arduino boards that you interconnect yourself. The main controller *must* be an Arduino MEGA, since we need multiple serial interfaces (UARTS). Depending on the number of buttons and lift levels, it might be possible to replace the boards for the Button and IR-sensor controllers by an Arduino UNO or NANO. This requires a number of software changes, however (primarily differen pin definitions)

The main controller takes care of DCC and RS-Bus messages. For the DCC and RS-Bus interfaces an option would be to use the [DCC and RS-Bus shield](https://oshwlab.com/aikopras/arduino-uno-dcc-shield). That shield includes all necessary DCC components, and allows connection of an [RS-Bus extension board](https://oshwlab.com/aikopras/rs-bus-tht).

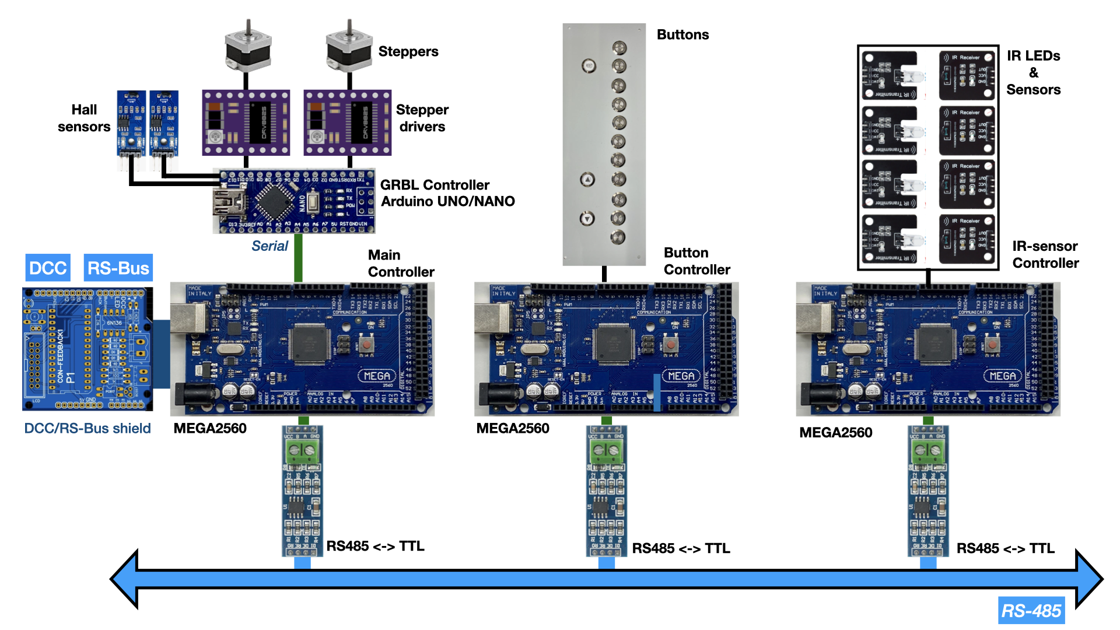
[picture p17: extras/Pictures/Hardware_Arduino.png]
Hardware-Arduino


How the different wires should be connected to the MEGA board, is shown in the following two pictures. If you want, possible pins for a Loconet interface are shown as well. Note, however, that Loconet software is not included and therefore has not been tested.
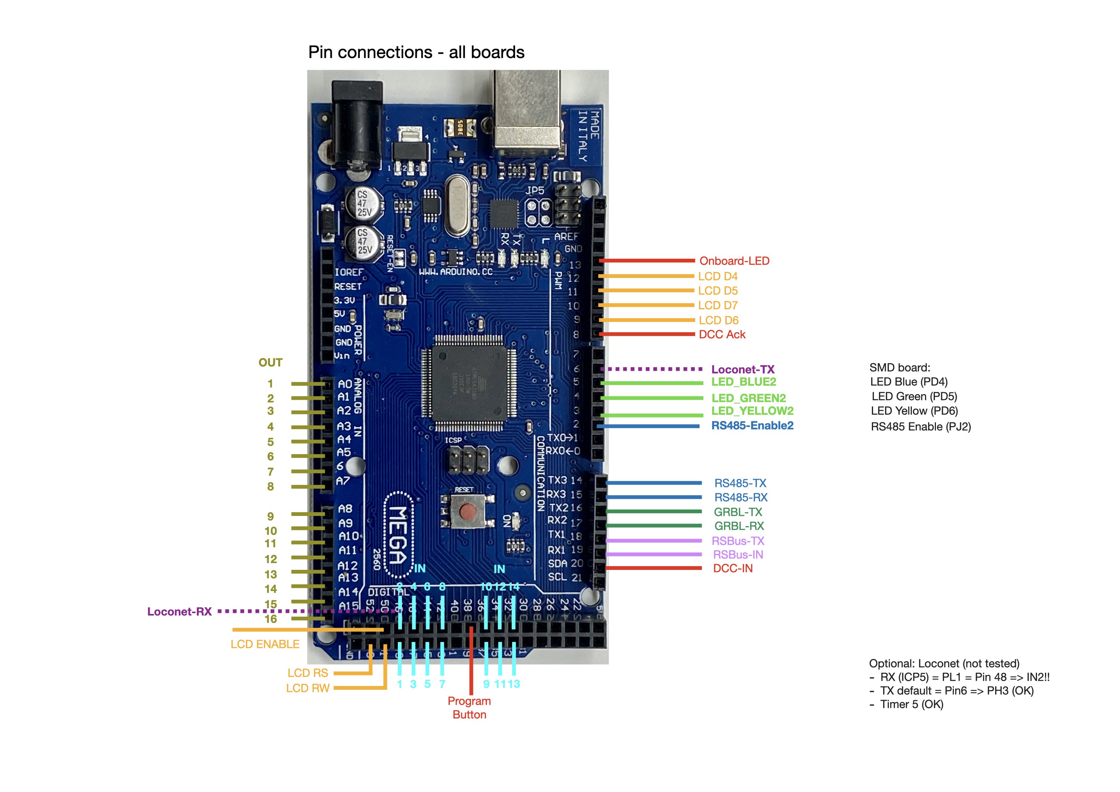
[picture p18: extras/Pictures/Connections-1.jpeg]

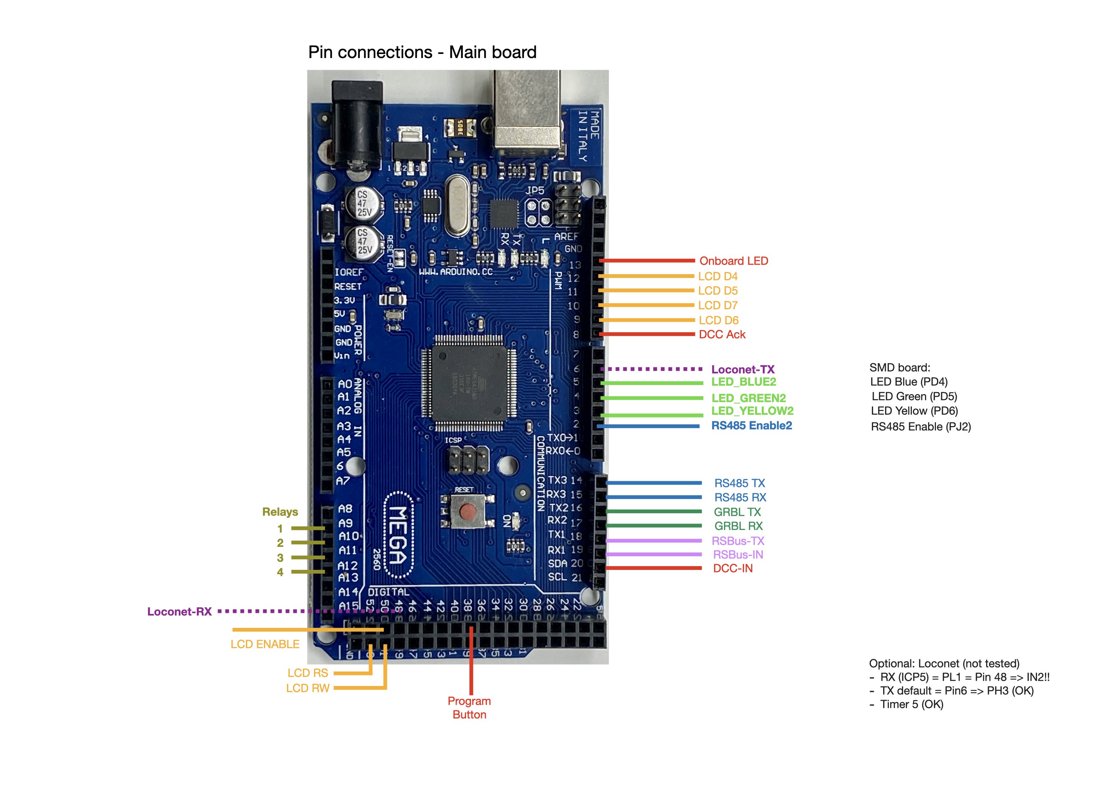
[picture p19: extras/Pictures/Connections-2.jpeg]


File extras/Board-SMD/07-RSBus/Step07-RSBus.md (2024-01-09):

## RSBus ##

Next step is testing the RSbus feedback interface. If you don't want your boards to send RSbus feedback messages, you may skip this step.

The schematics of the RSbus is shown in the figure below, and was derived from the description on the [Der Moba](http://www.der-moba.de/index.php/RS-Rückmeldebus) website.
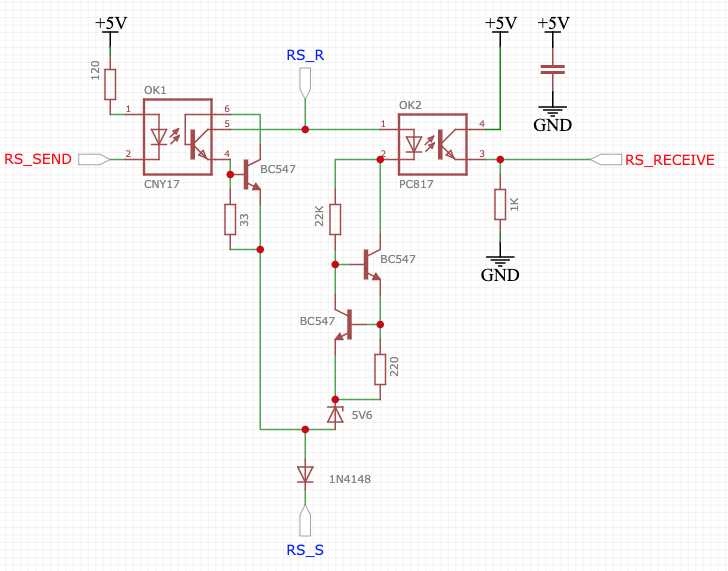
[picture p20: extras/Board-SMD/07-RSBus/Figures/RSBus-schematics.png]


A description on how to test the RSbus can be found in the examples section of the  [RSbus library](https://github.com/aikopras/RSbus). Follow the instructions on that page to install the library, in case it has not yet been installed.

Open the Arduino IDE. Select File -> Examples -> RSbus -> Monitor (see figure below).
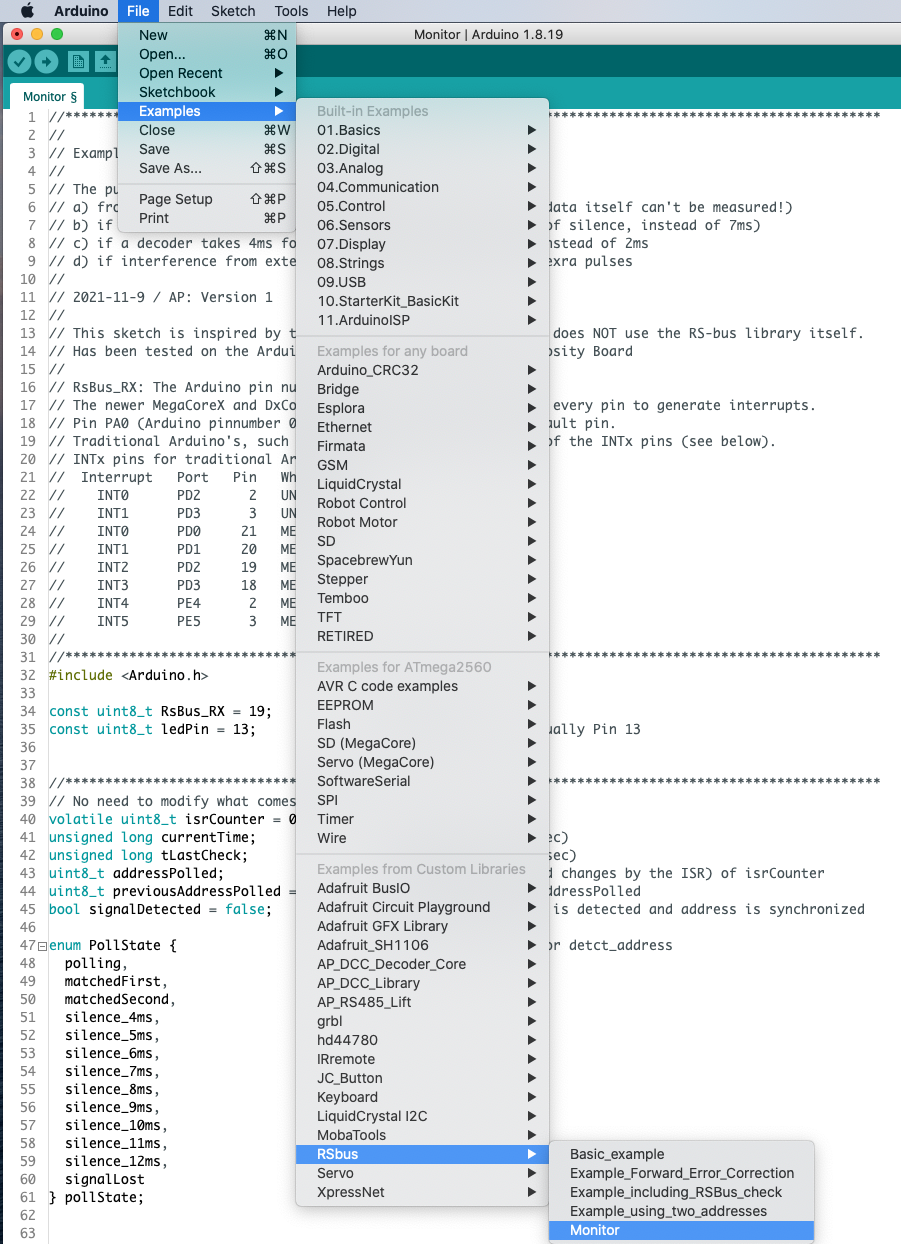
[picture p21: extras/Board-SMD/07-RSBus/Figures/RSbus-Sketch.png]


<BR>
Make sure you enter the right value for the RsBus_RX pin that receives the RSbus signal. For the Arduino ATMega 2560 processor, this must be Pin 19.
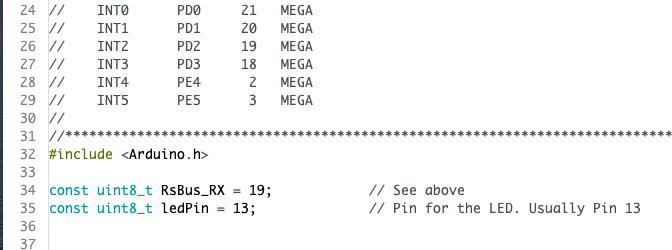
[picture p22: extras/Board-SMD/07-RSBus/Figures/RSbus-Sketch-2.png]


<BR>

[Compile and upload the sketch](../Compile.md). Open the Arduino Serial Monitor, and make  changes somewhere that trigger RSbus feedback messages. If things work well, you should see something like below.
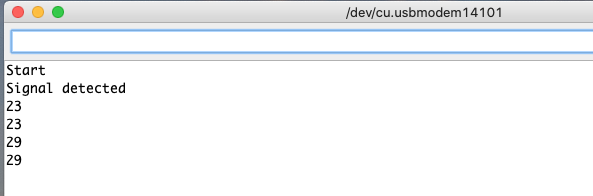
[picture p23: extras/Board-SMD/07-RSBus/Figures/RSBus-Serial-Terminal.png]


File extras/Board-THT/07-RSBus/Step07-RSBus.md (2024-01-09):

## RSBus ##

Next step is testing the RSbus feedback interface. If you don't want your boards to send RSbus feedback messages, you may skip this step.

The schematics of the RSbus is shown in the figure below, and was derived from the description on the [Der Moba](http://www.der-moba.de/index.php/RS-Rückmeldebus) website.


### PCBs ###
The THT Lift decoder board does ***not*** include the hardware for the RSbus, but allows to (later) add that hardware using so-called Piggy-back PCBs. These PCBs can be found on OSHWLab. There are two versions: a [THT version](https://oshwlab.com/aikopras/rs-bus-tht) and a [SMD version](https://oshwlab.com/aikopras/rs-bus-smd).

<table><tr>
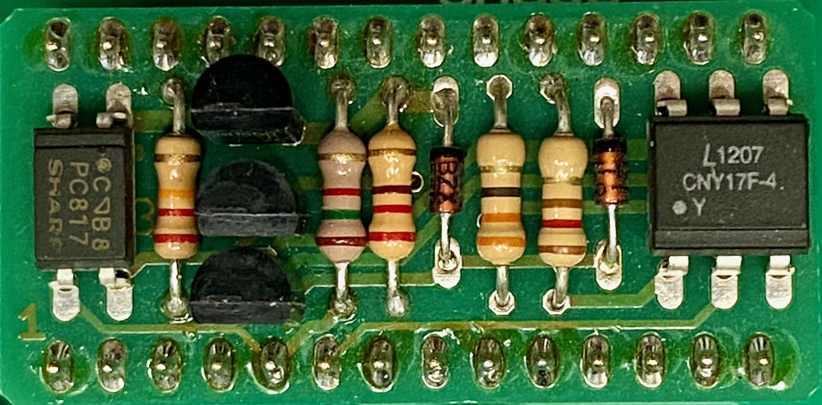
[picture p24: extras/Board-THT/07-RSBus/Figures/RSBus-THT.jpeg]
THT version
<td>  </td>
</tr></table>

### Testing ###
A description on how to test the RSbus can be found in the examples section of the  [RSbus library](https://github.com/aikopras/RSbus). Follow the instructions on that page to install the library, in case it has not yet been installed.

Open the Arduino IDE. Select File -> Examples -> RSbus -> Monitor (see figure below).


<BR>
Make sure you enter the right value for the RsBus_RX pin that receives the RSbus signal. For the Arduino ATMega 2560 processor, this must be Pin 19.


<BR>

[Compile and upload the sketch](../Compile.md). Open the Arduino Serial Monitor, and make  changes somewhere that trigger RSbus feedback messages. If things work well, you should see something like below.


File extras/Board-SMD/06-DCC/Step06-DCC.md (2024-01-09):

## DCC input ##

Next is testing that part of the board that is responsible for converting the DCC input signal into something that can be interpreted by the processor. If you don't want your lift to be controlled by DCC, you may skip this step.

The schematics of the DCC input part is shown in the figure below, and is quite standard for DCC decoding.
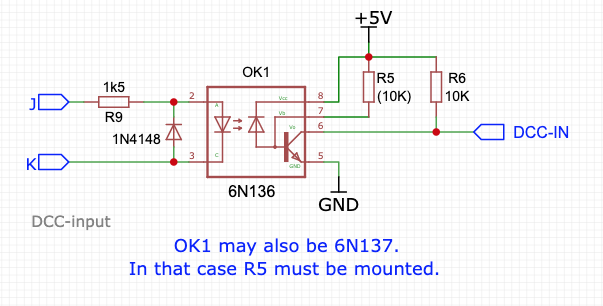
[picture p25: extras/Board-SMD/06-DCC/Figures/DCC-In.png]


A description on how to test DCC input can be found in the examples section of the  [AP_DCC_library](https://github.com/aikopras/AP_DCC_library). Follow the instructions on that page to install the library, in case it has not yet been installed.

Open the Arduino IDE. Select File -> Examples -> AP_DCC_Library -> Loco-Serial-monitor (see figure below).
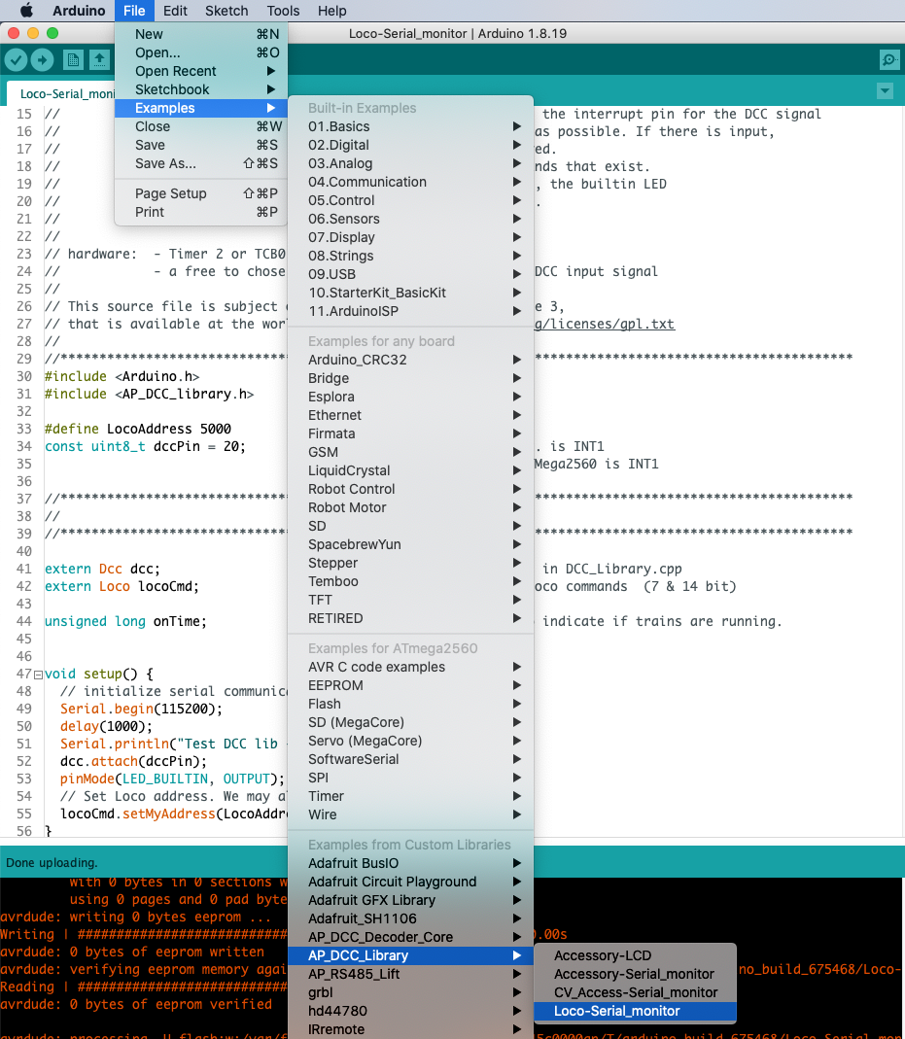
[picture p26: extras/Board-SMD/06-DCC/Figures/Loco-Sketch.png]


<BR>
Select the DCC loco address you want to monitor and make sure you enter the right value for the dccPin that receives the DCC signal. For the Arduino ATMega 2560 processor, this must be Pin 20.


<BR>

[Compile and upload the sketch](../Compile.md). Open the Arduino Serial Monitor, and use your handheld to make changes for this loco address. If things work well, you should see something like below.
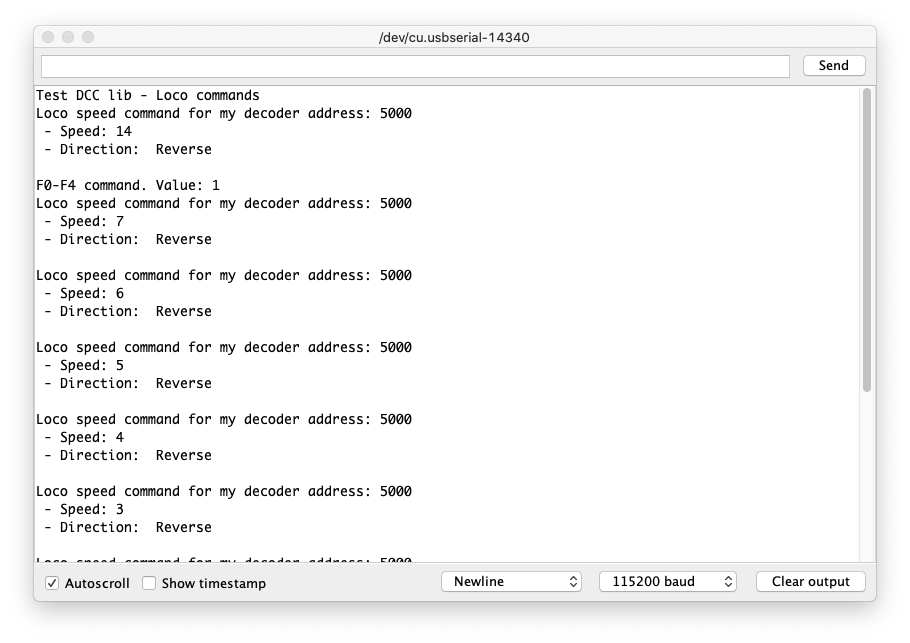
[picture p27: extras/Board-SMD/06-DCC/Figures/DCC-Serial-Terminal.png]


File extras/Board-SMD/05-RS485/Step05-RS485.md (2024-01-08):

## RS485 ##

After GRBL has been installed and tested, the next step is to test the RS485 connection between the three boards (Main, Button and IR-Sensor.)

Installation and testing of the RS485 bus is described as part of the [AP_RS485_Lift library](https://github.com/aikopras/AP_RS485_for_Lift_decoders). Follow the instructions there.

First, test with two boards only: the RS485 master and a single slave. After that you can connect a second slave, and test if communication is still possible with three devices attached. Don't forget to modify the RS485 addresses for testing the second slave.

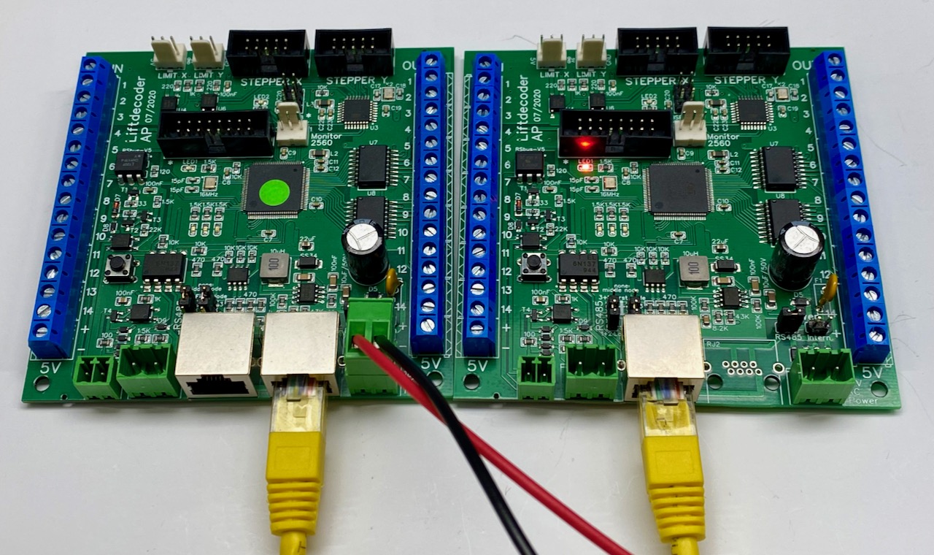
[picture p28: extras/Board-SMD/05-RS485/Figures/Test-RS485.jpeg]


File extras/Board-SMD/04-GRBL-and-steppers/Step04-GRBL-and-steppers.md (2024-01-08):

## Test the Stepper motors and Configure GRBL

The lift decoder board includes two processors: an ATMega 2560 for the main functions, and an ATMega 328 for GRBL.
The goal this step is to install and configure GRBL on the ATMega 328 processor.
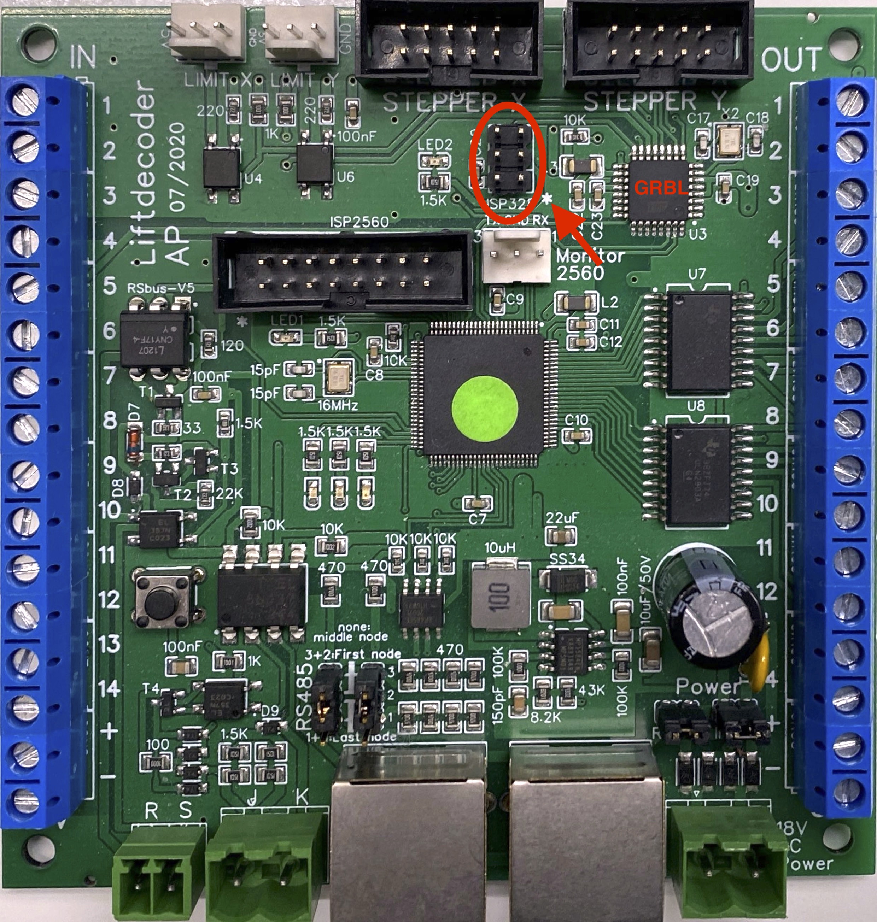
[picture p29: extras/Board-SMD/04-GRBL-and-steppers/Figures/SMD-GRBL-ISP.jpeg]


### Prepare GRBL ###
Instructions on how to compile GRBL can be found on the [GRBL Wiki](https://github.com/gnea/grbl/wiki/Compiling-Grbl).<BR>
Before compiling, a few changes may be required to the GRBL config.h file to ensure homing of the lift will operate as expected. Homing is generally needed to ensure that, after startup, the lift will be in a defined well-known position.<BR>
The default GRBL homing sequence is to first home the Z-axis (HOMING_CYCLE_0) and after that the X- and Y-axis together (HOMING_CYCLE_1). Since we don't have a Z-axis, we need to edit the GRBL config.h file to disable Z-axis homing and, instead, do the X- and Y-axis in the first cycle  (HOMING_CYCLE_0).<BR>
A second modification that is needed, is to change the origin, such that the lift operates in positive coordinate space. GRBL's default value is to operate into negative space, which seems to be typical for professional CNC machines. The code blocks below shows the changes I've made in GRBL's config.h file.<BR>
First disable the default lines for homing.

    // Disable following three lines for Loklift
    // #define HOMING_CYCLE_0 (1<<Z_AXIS)                // REQUIRED: First move Z to clear workspace.
    // #define HOMING_CYCLE_1 ((1<<X_AXIS)|(1<<Y_AXIS))  // OPTIONAL: Then move X,Y at the same time.
    // #define HOMING_CYCLE_2                            // OPTIONAL: Uncomment and add axes mask to enable

Second, create the new line for homing. If you have two stepper (X and Y), add the following:

    #define HOMING_CYCLE_0 ((1<<X_AXIS)|(1<<Y_AXIS))  // Homes both X-Y in the first cycle.

If you have a single stepper (X), add the following:

    #define HOMING_CYCLE_0 (1<<X_AXIS)            // Homes X in the first cycle.

Finally, uncomment the following line to use positive coordinates:

    // Enable the following line for Loklift
    #define HOMING_FORCE_SET_ORIGIN // Uncomment to enable.

For completeness, the [new config.h file](GRBL_config/config.h) is included in the folder [GRBL_config](GRBL_config)

### Compile GRBL (v1.1) ###
After GRBL has been downloaded and the config.h file has been modified, GRBL can be compiled and uploaded to the ATMega 328 processor. Connect your programmer (such as USBasp) to the 6 pin connector called ISP328. Take care that the programmer's MISO pin (1) is connected to the pin that is marked (*). On the Arduino IDE, select as board "Arduino UNO", and as programmer "USBasp", or whatever programmer you have.
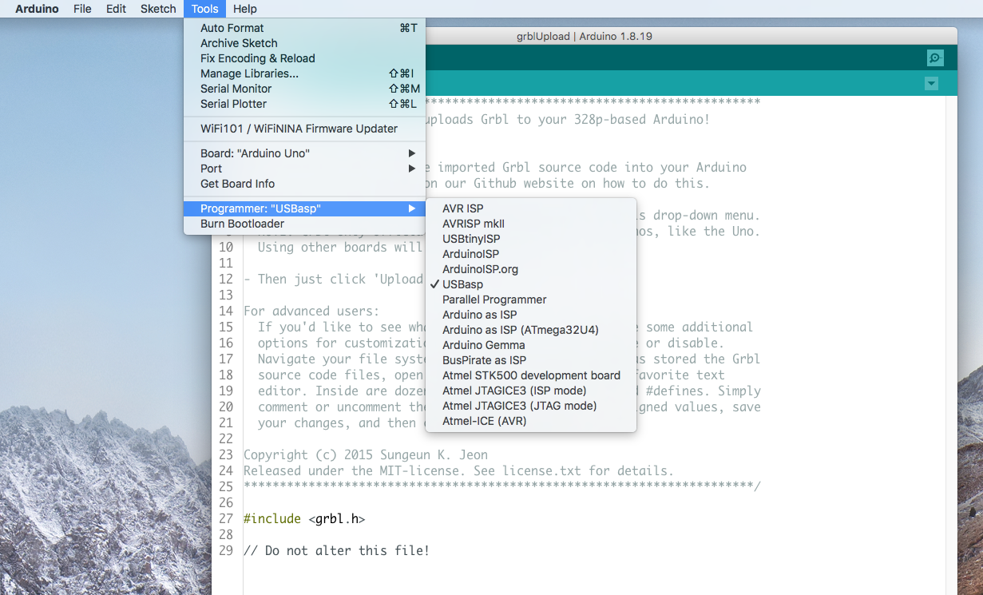
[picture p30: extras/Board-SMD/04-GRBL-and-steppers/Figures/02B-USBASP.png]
 

### Upload GRBL (v1.1) ###
To flash the GRBL code, select "Upload Using programmer". While programming, a small red LED on the decoder board will blink.
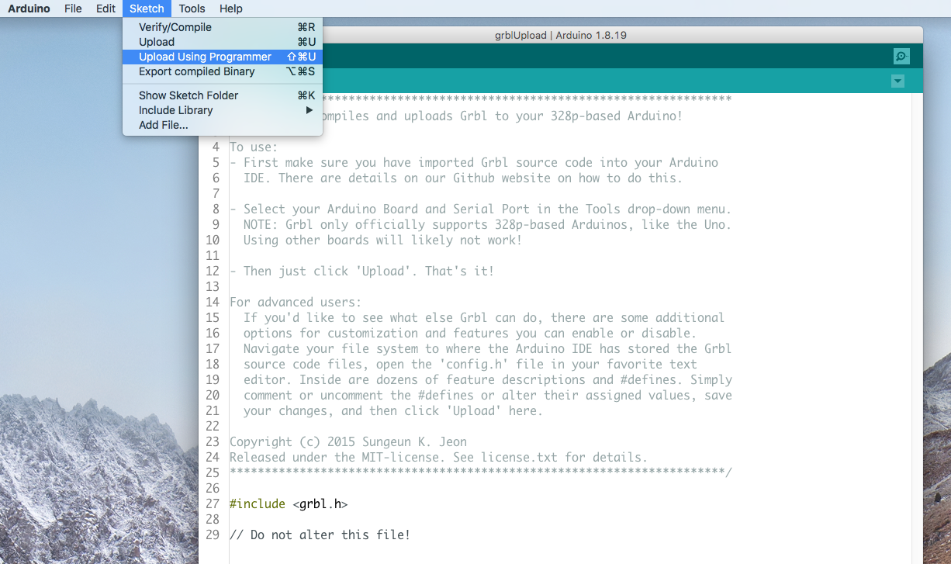
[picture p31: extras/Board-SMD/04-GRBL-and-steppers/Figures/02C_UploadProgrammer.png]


### Connect the stepper driver(s) and stepper motor(s) ###
You may use one or two Steppers, and connect them as Stepper X and / or Stepper Y.
An example of a good driver is the Makerbase MKS TMC2160. Alternatively you can use so-called StepStick drivers, such as the A4988, DRV8825, or the TMC2209 SilentStep Stick. Compared to the A4988 and DRV8825, the TMC2160 and 2209 make considerable less noise. If you prefer the StepStick drivers, you could consider the [opto-decoupled TMC 2209 driver board](https://oshwlab.com/aikopras/tmc2209-driver-board). The connector of that board is the same as used on the lift decoder board. On the Lift decoder board, connect the drivers to the connectors called STEPPER X (and STEPPER Y). The pins of these connectors follow the so-called [PMinMo 'standard'](http://www.massmind.org/techref/io/PMinMO.htm).
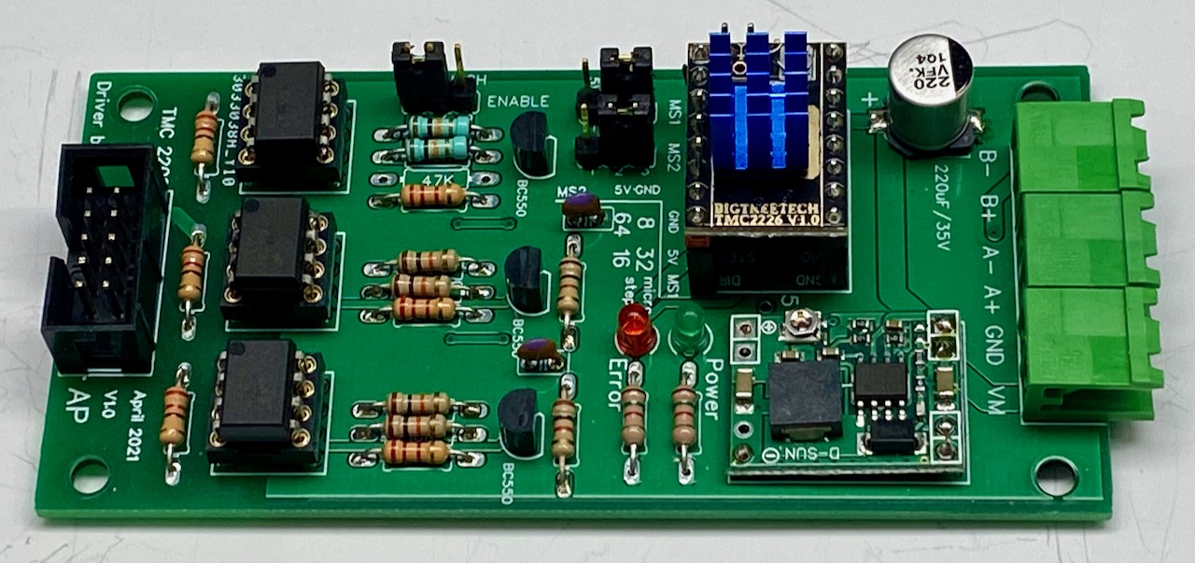
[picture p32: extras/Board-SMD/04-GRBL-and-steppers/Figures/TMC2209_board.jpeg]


### Test the stepper(s) ###
Sending GRBL commands to test the stepper motor(s) can be done using the Serial monitor of the Arduino IDE. You therefore need a serial (USB) connection between your computer and the ATMega 328. However, the ATMega 328 processor on the lift decoder board has no USB connector attached to it. Therefore, we will send GRBL commands via the serial interface attached to the ATMega 2560 processor. For that purpose we need to install a simple sketch onto the ATMega 2560 processor, that mirrors all communications. Open the sketch [04-Configure_GRBL_and_test_steppers.ino](../../../Tests/04-Configure_GRBL_and_test_steppers/04-Configure_GRBL_and_test_steppers.ino) and upload it to the ATMega 2560 processor.

Use the Arduino "Serial Monitor" (or whatever program you have that supports serial communication) and set the baudrate to 115200. Test GRBL, by typing GRBL commands such as "?" and "$$". If you receive responses from GRBL, check next if the stepper motor is running, by using commands such as "X10" or X"0". See below for some of the main GRBL commands; a number of examples can be found in the file [GRBL-test-example.rtf](GRBL-test-example/GRBL-test-example.rtf):
- **?** - Status report query
- **X*value*** - Move the X stepper motor to *value*
- **X10 Y10** - Move the X and Y stepper motors to position 10mm
- **$$** - Display Grbl Settings
- **$H** - Run Homing Cycle
- **$X** - Cancel Alarm Lock state
- **Ctrl-x** - Soft Reset

### Configure the GRBL variables ###
The next, important step, is to configure the GRBL variables. If these variables are not configured well, the lift will most likely not operate as expected. A detailed description of these variable is provided on the [GRBL wiki](https://github.com/gnea/grbl/wiki/Grbl-v1.1-Configuration). Important variables that you most likely will have to change are **X/Y steps** ($100, $101), **X/Y Max rate** ($110, $111) as well as **X/Y Max travel**. Also **Direction invert** ($3) may have to be modified, if the lift moves in the opposite direction.

### Homing ###
The final big step in configuring GRBL, is **Homing**. Homing is needed to guarantee that, after the system has started, the lift moves to a well-defined position. The configuration variables relevant for Homing are: **Enable Homing** ($22=1), **Homing pull-off** ($27), the **Homing direction** ($23) and **Homing rate** ($24). Some additional details can be found on the GRBL wiki.
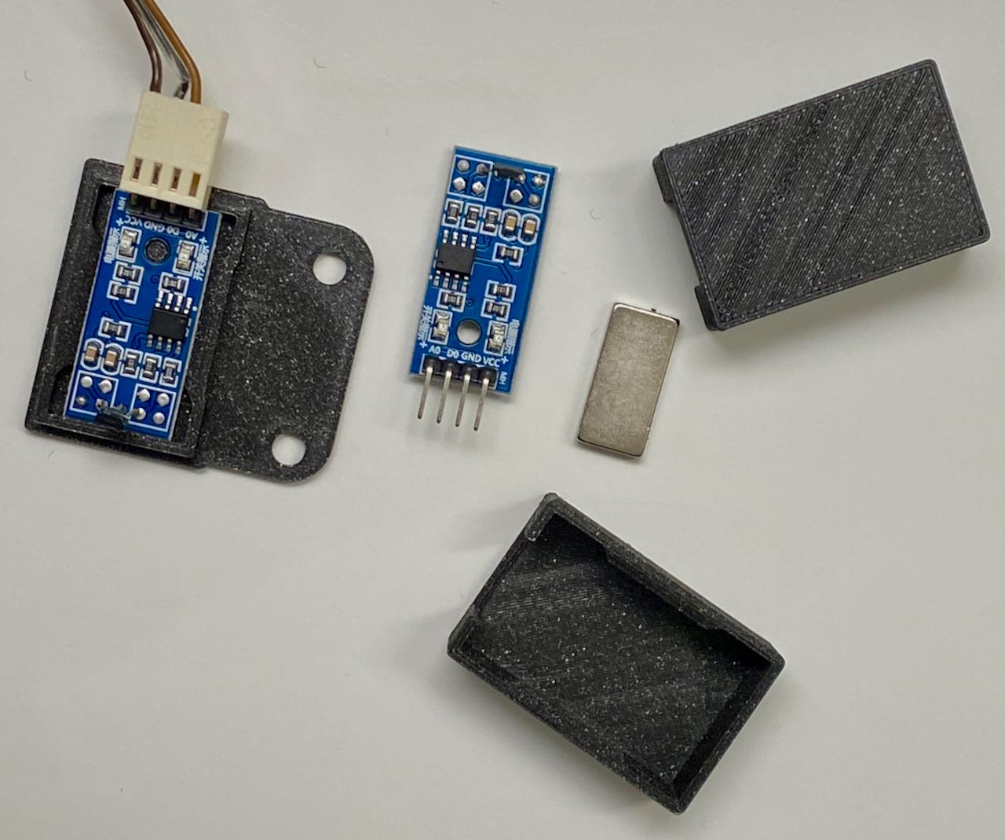
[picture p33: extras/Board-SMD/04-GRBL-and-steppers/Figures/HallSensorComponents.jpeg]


The picture above shows the (Chinese) Hall sensors and magnets I've used for homing. The picture also shows the holders that were 3D-printed to mount the Hall sensor and magnet. I've  [added the STL files](3D_Hall-sensor/) in case you want to print these yourself. The Hall sensor modules should be connected to the **Limit-X** and **Limit-Y** connectors on the lift decoder board. **VCC** should be connected to the pin labelled **5V**, **GND** to **GND** and **DO** to the connector's middle pin.

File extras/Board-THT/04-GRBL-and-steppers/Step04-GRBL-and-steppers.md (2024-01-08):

## Test the Stepper motors and Configure GRBL

The THT lift decoder board has space for two Arduino's: an Arduino MEGA 2560 for the main functions, and an Arduino NANO for GRBL.
The goal this step is to install and configure GRBL on the Arduino NANO.
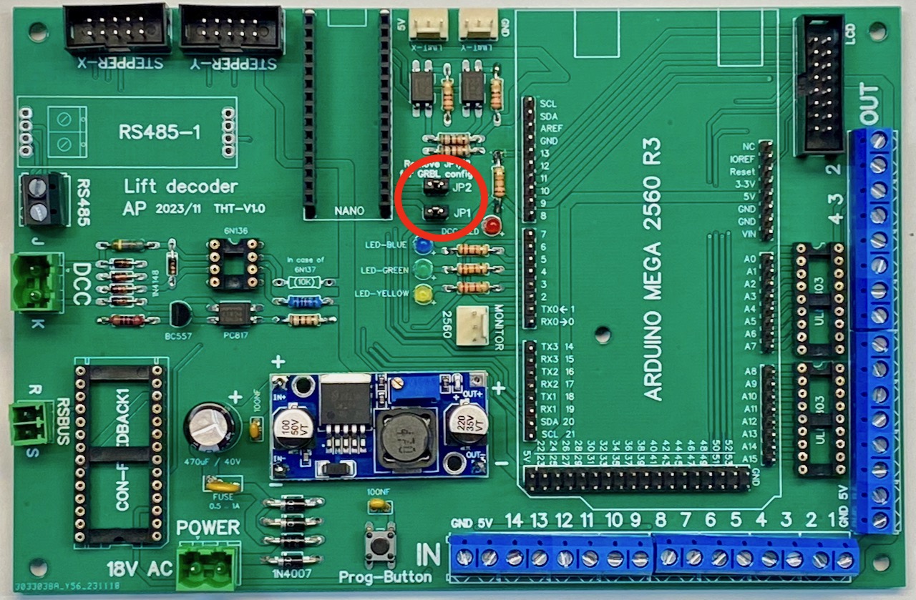
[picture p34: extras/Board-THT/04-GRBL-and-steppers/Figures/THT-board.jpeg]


### Prepare GRBL ###
Instructions on how to compile GRBL can be found on the [GRBL Wiki](https://github.com/gnea/grbl/wiki/Compiling-Grbl).<BR>
Before compiling, a few changes may be required to the GRBL config.h file to ensure homing of the lift will operate as expected. Homing is generally needed to ensure that, after startup, the lift will be in a defined well-known position.<BR>
The default GRBL homing sequence is to first home the Z-axis (HOMING_CYCLE_0) and after that the X- and Y-axis together (HOMING_CYCLE_1). Since we don't have a Z-axis, we need to edit the GRBL config.h file to disable Z-axis homing and, instead, do the X- and Y-axis in the first cycle  (HOMING_CYCLE_0).<BR>
A second modification that is needed, is to change the origin, such that the lift operates in positive coordinate space. GRBL's default value is to operate into negative space, which seems to be typical for professional CNC machines. The code blocks below shows the changes I've made in GRBL's config.h file.<BR>
First disable the default lines for homing.

    // Disable following three lines for Loklift
    // #define HOMING_CYCLE_0 (1<<Z_AXIS)                // REQUIRED: First move Z to clear workspace.
    // #define HOMING_CYCLE_1 ((1<<X_AXIS)|(1<<Y_AXIS))  // OPTIONAL: Then move X,Y at the same time.
    // #define HOMING_CYCLE_2                            // OPTIONAL: Uncomment and add axes mask to enable

Second, create the new line for homing. If you have two stepper (X and Y), add the following:

    #define HOMING_CYCLE_0 ((1<<X_AXIS)|(1<<Y_AXIS))  // Homes both X-Y in the first cycle.

If you have a single stepper (X), add the following:

    #define HOMING_CYCLE_0 (1<<X_AXIS)            // Homes X in the first cycle.

Finally, uncomment the following line to use positive coordinates:

    // Enable the following line for Loklift
    #define HOMING_FORCE_SET_ORIGIN // Uncomment to enable.

For completeness, the [new config.h file](GRBL_config/config.h) is included in the folder [GRBL_config](GRBL_config)

### Compile and Upload GRBL (v1.1) ###
After GRBL has been downloaded and the config.h file has been modified, GRBL can be compiled and uploaded to the Arduino NANO board. Connect the Nano via USB to the computer running the Arduino IDE. On the Arduino IDE, select as board "Arduino UNO" (or, in my case, Arduino Pro), and the port.
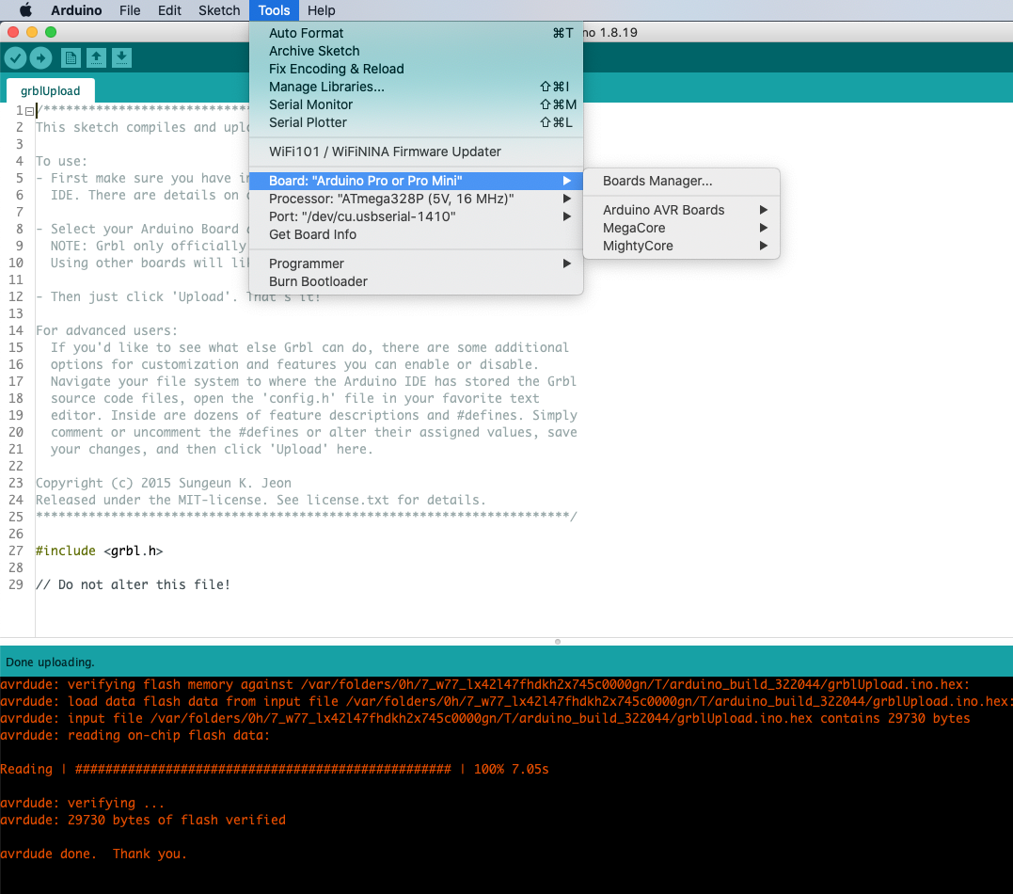
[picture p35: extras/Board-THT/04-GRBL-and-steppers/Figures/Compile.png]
 

### Connect the stepper driver(s) and stepper motor(s) ###
You may use one or two Steppers, and connect them as Stepper X and / or Stepper Y.
An example of a good driver is the Makerbase MKS TMC2160. Alternatively you can use so-called StepStick drivers, such as the A4988, DRV8825, or the TMC2209 SilentStep Stick. Compared to the A4988 and DRV8825, the TMC2160 and 2209 make considerable less noise. If you prefer the StepStick drivers, you could consider the [opto-decoupled TMC 2209 driver board](https://oshwlab.com/aikopras/tmc2209-driver-board). The connector of that board is the same as used on the lift decoder board. On the Lift decoder board, connect the drivers to the connectors called STEPPER X (and STEPPER Y). The pins of these connectors follow the so-called [PMinMo 'standard'](http://www.massmind.org/techref/io/PMinMO.htm).


### Test the stepper(s) ###
Sending GRBL commands to test the stepper motor(s) can be done using the Serial monitor of the Arduino IDE. There are two possibilities to test.
  - The first possibility is to use the USB connection to the Arduino Nano. In that case you have to remove the jumpers **JP1** and **JP2** on the THT lift decoder board. If you don't remove these jumpers, and you have the Arduino MEGA mounted, the communication channel between MEGA and NANO takes precedence over the NANO's USB connection. As a result, the NANO will no longer listen to the USB connection.
  - The second possibility is to use the USB connection on the Arduino MEGA. Make sure that the jumpers **JP1** and **JP2** are installed. Next you have to install a simple sketch onto the Arduino MEGA, that mirrors all communications from/to the MEGA's USB port to the Arduino NANO. Open the sketch [04-Configure_GRBL_and_test_steppers.ino](../../../Tests/04-Configure_GRBL_and_test_steppers/04-Configure_GRBL_and_test_steppers.ino) and upload it to the Arduino MEGA.

Use the Arduino "Serial Monitor" (or whatever program you have that supports serial communication) and set the baudrate to 115200. Test GRBL, by typing GRBL commands such as "?" and "$$". If you receive responses from GRBL, check next if the stepper motor is running, by using commands such as "X10" or X"0". See below for some of the main GRBL commands; a number of examples can be found in the file [GRBL-test-example.rtf](GRBL-test-example/GRBL-test-example.rtf):
- **?** - Status report query
- **X*value*** - Move the X stepper motor to *value*
- **X10 Y10** - Move the X and Y stepper motors to position 10mm
- **$$** - Display Grbl Settings
- **$H** - Run Homing Cycle
- **$X** - Cancel Alarm Lock state
- **Ctrl-x** - Soft Reset

### Configure the GRBL variables ###
The next, important step, is to configure the GRBL variables. If these variables are not configured well, the lift will most likely not operate as expected. A detailed description of these variable is provided on the [GRBL wiki](https://github.com/gnea/grbl/wiki/Grbl-v1.1-Configuration). Important variables that you most likely will have to change are **X/Y steps** ($100, $101), **X/Y Max rate** ($110, $111) as well as **X/Y Max travel**. Also **Direction invert** ($3) may have to be modified, if the lift moves in the opposite direction.

### Homing ###
The final big step in configuring GRBL, is **Homing**. Homing is needed to guarantee that, after the system has started, the lift moves to a well-defined position. The configuration variables relevant for Homing are: **Enable Homing** ($22=1), **Homing pull-off** ($27), the **Homing direction** ($23) and **Homing rate** ($24). Some additional details can be found on the GRBL wiki.


The picture above shows the (Chinese) Hall sensors and magnets I've used for homing. The picture also shows the holders that were 3D-printed to mount the Hall sensor and magnet. I've  [added the STL files](3D_Hall-sensor/) in case you want to print these yourself. The Hall sensor modules should be connected to the **Limit-X** and **Limit-Y** connectors on the lift decoder board. **VCC** should be connected to the pin labelled **5V**, **GND** to **GND** and **DO** to the connector's middle pin.

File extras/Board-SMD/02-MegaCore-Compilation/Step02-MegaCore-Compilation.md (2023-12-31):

## MegaCore - Compile and upload ##

The goal of this step is to install the MegaCore board in the Arduino IDE (*this description uses Version 1.8.19 of the IDE, but Version 2 is similar*).

The Lift Decoder software relies on various definitions and functions that are not available within the default Arduino environment, but are provided by MegaCore. Therefore we must install MegaCore first. For details regarding MegaCore, see: *[https://github.com/MCUdude/MegaCore](https://github.com/MCUdude/MegaCore)*. Installing megaCore requires a number of steps.

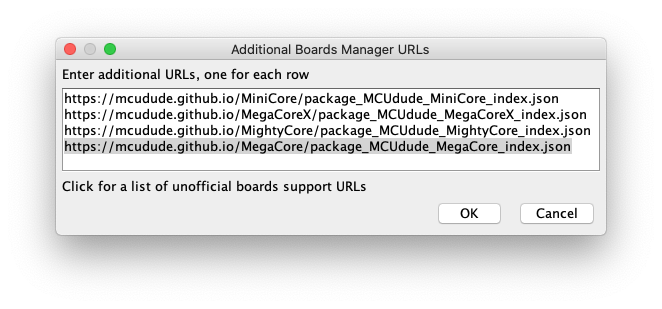
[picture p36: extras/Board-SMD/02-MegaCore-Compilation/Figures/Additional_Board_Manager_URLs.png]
First, ensure that the Arduino IDE can find the MegaCore board. Therefore you have to start the Arduino IDE and open **Preferences** and click **Additional Boards Manager URLs**. Add: **https://mcudude.github.io/MegaCore/package_MCUdude_MegaCore_index.json**. The result will be something like below:

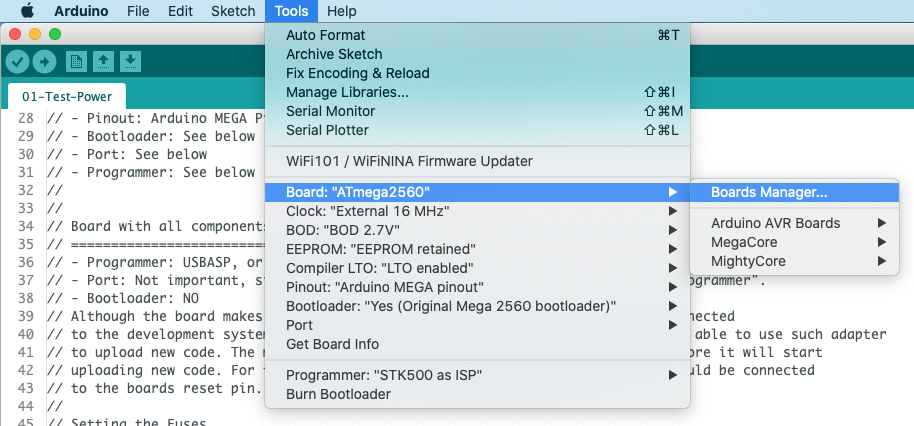
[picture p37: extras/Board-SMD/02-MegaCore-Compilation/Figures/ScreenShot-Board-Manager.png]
Second, install the MegaCore board. Go to **Tools/Board/Board Manager**.

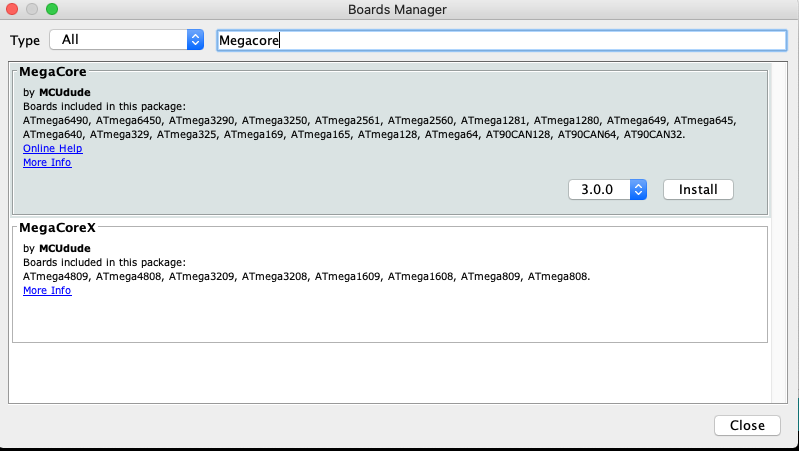
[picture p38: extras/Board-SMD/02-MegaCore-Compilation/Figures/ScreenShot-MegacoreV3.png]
In the window that opens, type **Megacore**. 

### Blink sketch ###
Next we will check if everything is working, by installing the blink test sketch. Therefore open the Blink sketch (File => Examples => 01.Basics). The end result should be a blinking LED.

Although the board makes UART0 available as monitoring port, which can be connected to a development system via a serial to usb adapter, in general we won't be able to use such adapter to upload new code. The main reason is that bootloaders require a RESET before they start uploading new code. For this to happen the DTR signal of a serial adapter should be connected to the board's reset pin. Most adapters don't export such DTR signal, however.

Therefore uploading of sketches has to be done using an external programmer, such as USBasp. This programmer has been developed by [Thomas Fischl](https://www.fischl.de/usbasp/), and can be bought at various places. Alternatively it is also possible to use a [second Arduino as programmer](https://docs.arduino.cc/built-in-examples/arduino-isp/ArduinoISP).

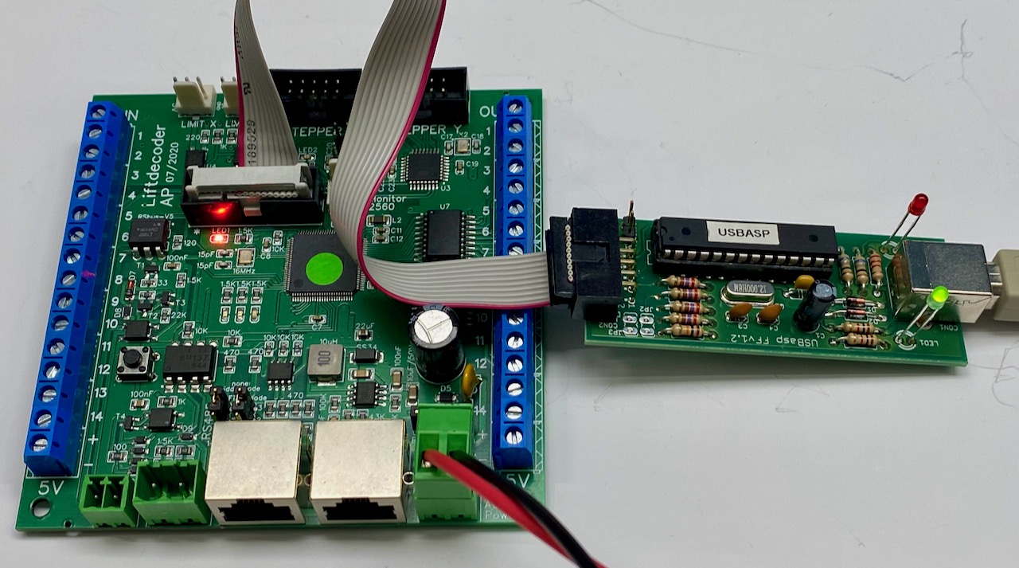
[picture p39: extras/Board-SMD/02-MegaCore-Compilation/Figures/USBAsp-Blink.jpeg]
The programmer must be connected to the 16 pin ISP connector on the decoder board. See the figure below. 

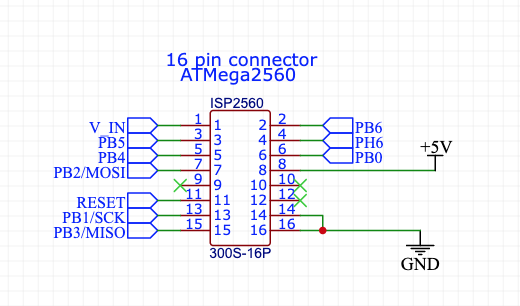
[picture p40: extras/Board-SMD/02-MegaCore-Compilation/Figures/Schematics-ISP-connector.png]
 The figure above shows how the pins of the 16-pin connector are wired. For programming, only the pins 7 till 16 are used.

<P>

Before we can upload any sketch, we need to initialize the fuse bits. This can be done by selecting in the Arduino IDE **Tools/Burn Bootloader**. This command may look a bit misleading, since if we don't select a bootloader, only the fuse bits will be set. Setting the fuse bits is needed only once, when the processor gets programmed first.

Alternatively we may also use the development system's command line to issue the following command (assuming usbasp): **avrdude -c usbasp -p m2560 -U lfuse:w:0xEE:m -U hfuse:w:0xD9:m -U efuse:w:0xFE:m**.

### Compile and upload sketch ###
To compile and upload a sketch, select the MegaCore board, the ATmega 2560 processor, MEGA pinout, and "no bootloader"; for the other settings see below. Select the programmer you have. Upload the sketch (**Upload** button or **Sketch => Using Programmer**).


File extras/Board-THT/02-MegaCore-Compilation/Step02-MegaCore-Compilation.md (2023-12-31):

## MegaCore - Compile and upload ##

The goal of this step is to install the MegaCore board in the Arduino IDE (*this description uses Version 1.8.19 of the IDE, but Version 2 is similar*).

The Lift Decoder software relies on various definitions and functions that are not available within the default Arduino environment, but are provided by MegaCore. Therefore we must install MegaCore first. For details regarding MegaCore, see: *[https://github.com/MCUdude/MegaCore](https://github.com/MCUdude/MegaCore)*. Installing megaCore requires a number of steps.

First, ensure that the Arduino IDE can find the MegaCore board. Therefore you have to start the Arduino IDE and open **Preferences** and click **Additional Boards Manager URLs**. Add: **https://mcudude.github.io/MegaCore/package_MCUdude_MegaCore_index.json**. The result will be something like below: 

Second, install the MegaCore board. Go to **Tools/Board/Board Manager**.

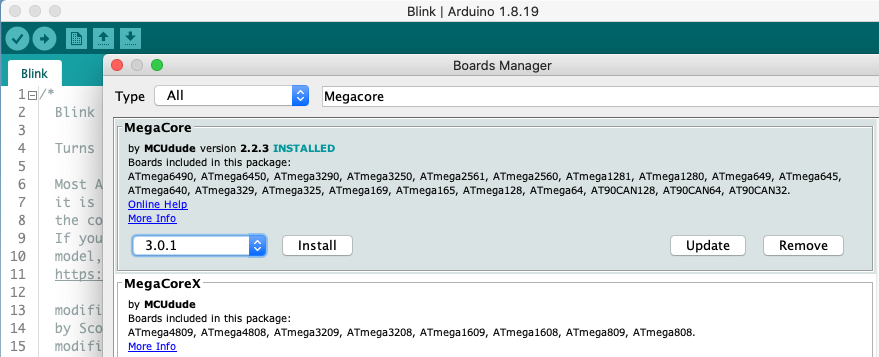
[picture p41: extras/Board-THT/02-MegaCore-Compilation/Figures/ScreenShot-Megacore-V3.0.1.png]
In the window that opens, type **Megacore**. 

**Note:** Be sure to install V3.0.1 or higher (V3.0.0 of the MegaCore board lacked support for the original Arduino Mega bootloader).

### Blink sketch ###
Next we will check if everything is working, by installing the blink test sketch. Therefore open the Blink sketch (File => Examples => 01.Basics). The end result should be a blinking LED.

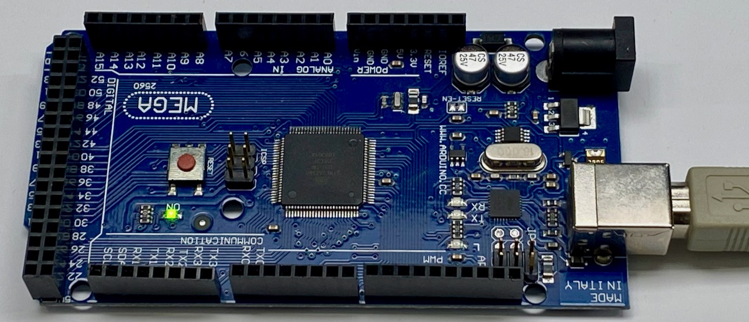
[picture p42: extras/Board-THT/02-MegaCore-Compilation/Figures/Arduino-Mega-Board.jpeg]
Connect a USB cable to the Arduino Mega boards 

### Compile and upload sketch ###
To compile and upload a sketch, select the MegaCore board, the ATmega 2560 processor and as Programmer the "Legacy Arduino MEGA bootloader". See below for the other settings. Upload the sketch (**Upload** button).


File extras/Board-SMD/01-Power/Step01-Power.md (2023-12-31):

## Power the board

The goal of this step is to test if the power electronics (step-down converter) works well.

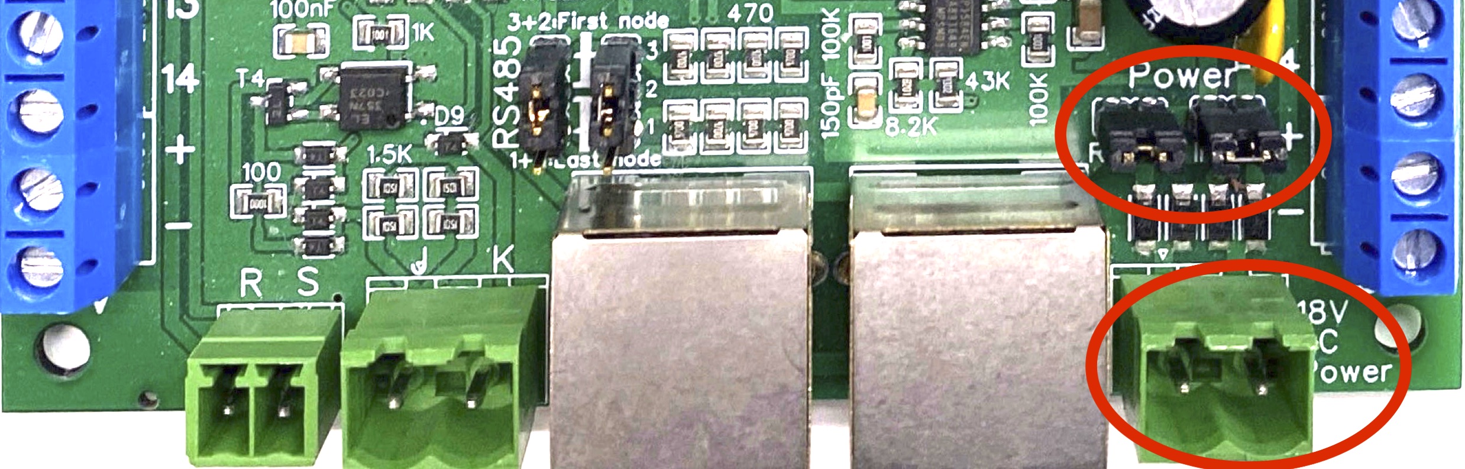
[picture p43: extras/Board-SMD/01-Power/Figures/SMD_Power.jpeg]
Connect a power supply to the connector labelled **18V AC Power**. The power supply should deliver anything between 8 and 24V; a DC power supply should also work. In addition, connect the jumper "intern", to ensure the external power is used internally for the board. 

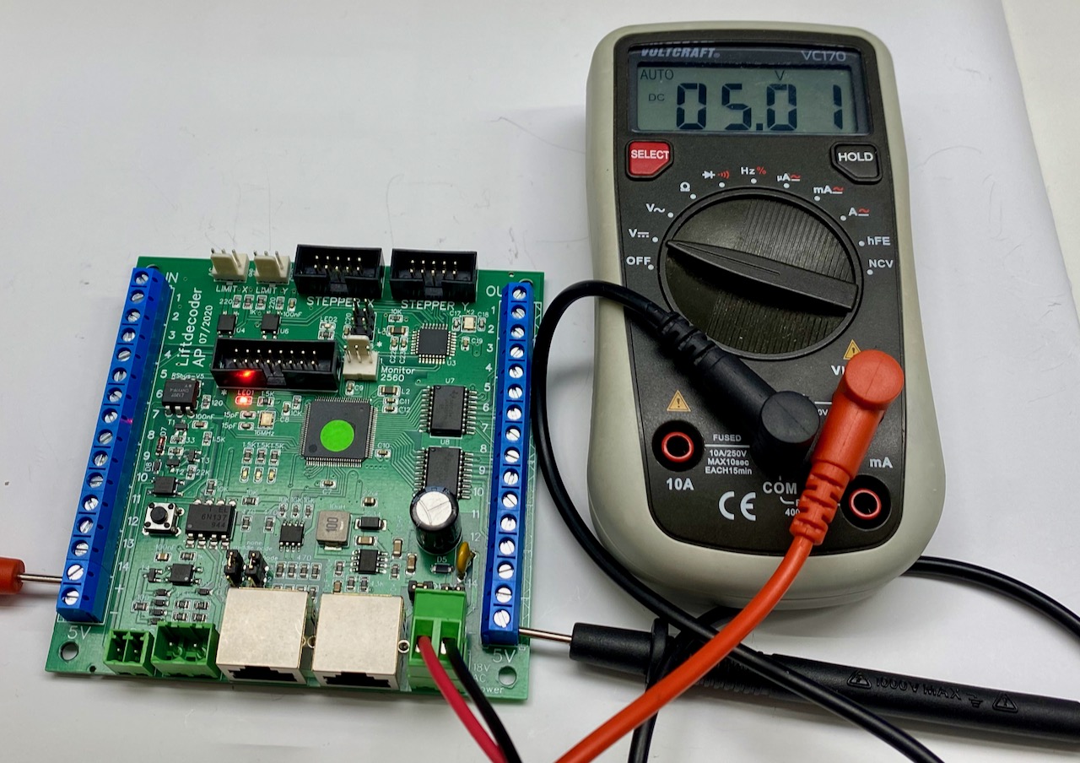
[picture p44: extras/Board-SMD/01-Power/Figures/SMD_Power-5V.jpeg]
Next you may check if the power is indeed 5V. Connect a voltmeter to (for example) the blue connectors labelled **5V +** and **5V -**. The voltmeter should show (around) 5Volt.

The second jumper called **RS-485** forwards the incoming power additionally over the "RS-485 bus" towards possible additional lift decoder boards (which can be used to control the button and/or IR-Sensors). The goal of this is to simplify the wiring of the power towards multiple boards. These additional boards receive their power via a network cable, connected to the the RJ45 connector (see below).

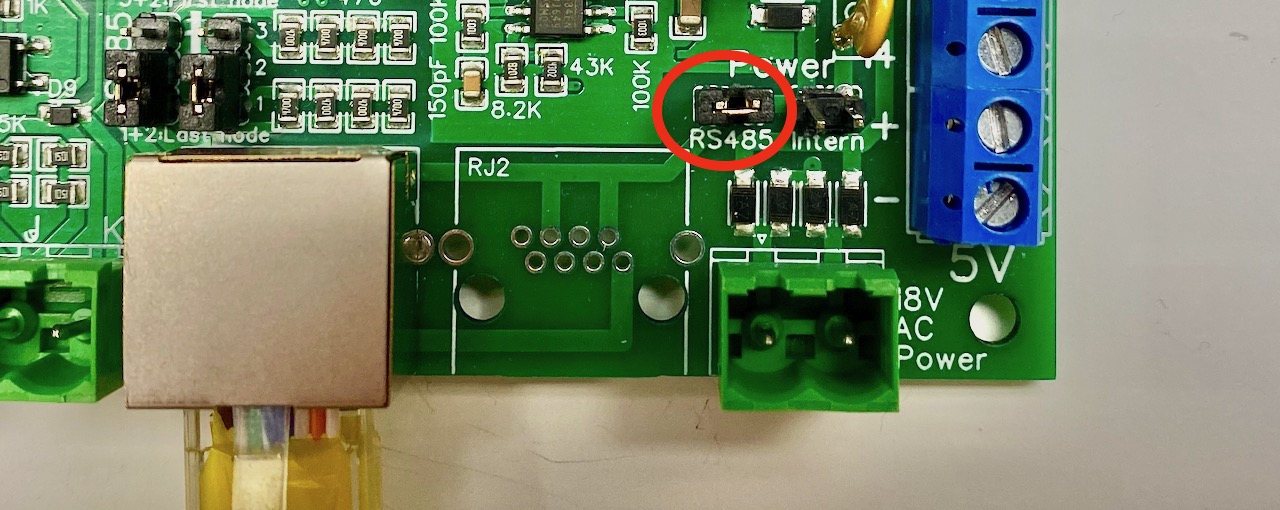
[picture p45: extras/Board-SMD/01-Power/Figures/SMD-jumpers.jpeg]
The additional boards should also have the jumper **RS-485** installed, to ensure that the power that comes in via the network cable gets forwarded to the onboard step-down converter. It is recommended to check also the step-down converters on the other boards for 5V.

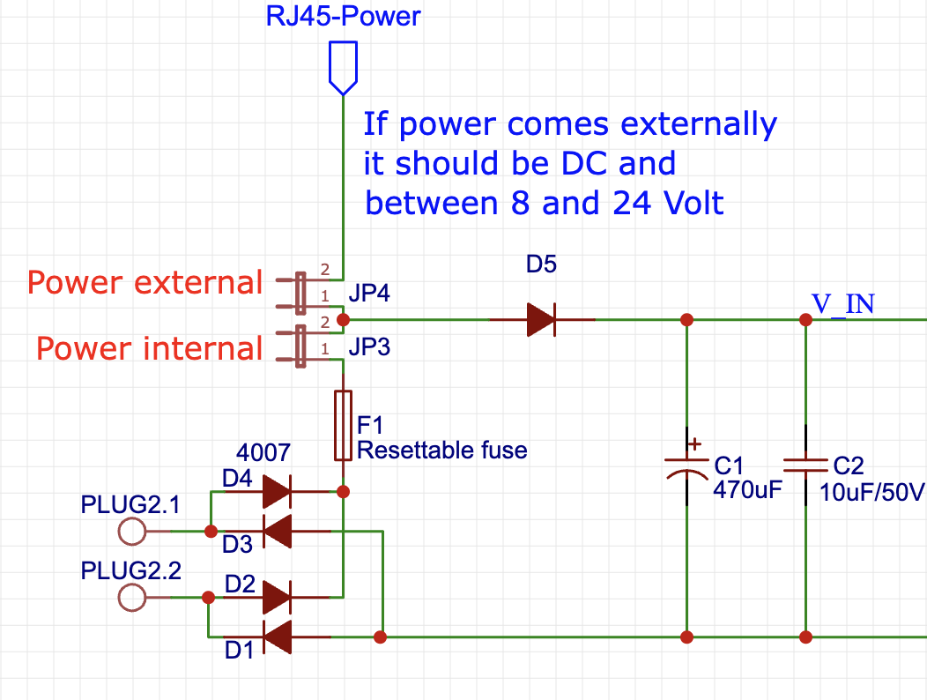
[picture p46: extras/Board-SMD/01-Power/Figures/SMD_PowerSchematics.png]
For clarity, the figure below shows the part of the board's schematics that shows the power jumpers.

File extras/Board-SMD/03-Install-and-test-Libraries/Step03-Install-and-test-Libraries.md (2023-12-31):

## Install and test the required Libraries

The goal of this step is to install and test all required libraries.

* AP_DCC_library: https://github.com/aikopras/AP_DCC_library<br>
This library contains all the code needed to decode the DCC signal. If you don't want to connect your lift decoder to a DCC system, you should still install this library.
* RSbus library: https://github.com/aikopras/RSbus<br>
This library contains all the code needed to send RS-Bus feedback signals. If you don't use the RS-Bus for feedback, you should still install this library.
* AP_RS485_Lift library: https://github.com/aikopras/AP_RS485_for_Lift_decoders<br>
A small library responsible for the communication between the various lift decoder boards. If you don't need the button and IR-sensor decoders, you should still install this library.
* AP_DCC_Decoder_Core library: https://github.com/aikopras/AP_DCC_Decoder_Core<br>
This library creates a decoder skeleton. It handles CV values and programming.
* MobaTools: https://github.com/MicroBahner/MobaTools<br>
From this library we only use the timers.

A description of how to install libraries see the related [Arduino documentation](https://docs.arduino.cc/software/ide-v1/tutorials/installing-libraries). Note that the AP_RS485_Lift and AP_DCC_Decoder_Core library must be manually downloaded from Github and installed at the right place in your Arduino Library folder. the other libraries can be found via the Arduino Library manager.

### The Test Libraries script ###
Open the sketch 03-Test-Libraries.ino (in the **Tests** folder). Compile and upload the sketch, using the settings as explained earlier in [Step02-Install-and-test-MegaCore.md](../02-Install-and-test-MegaCore/Step02-Install-and-test-MegaCore.md).

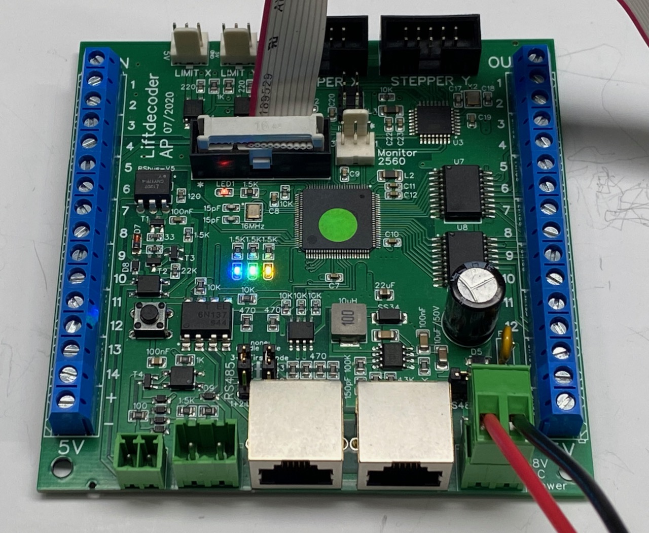
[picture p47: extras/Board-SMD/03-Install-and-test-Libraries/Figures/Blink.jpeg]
For the test to be successful, no compile errors may be raised, upload should work and all LEDs should blink, thus the red (onboard / DCC), blue, green and yellow LED. See the figure below.

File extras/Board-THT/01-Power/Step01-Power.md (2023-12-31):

## Power the board

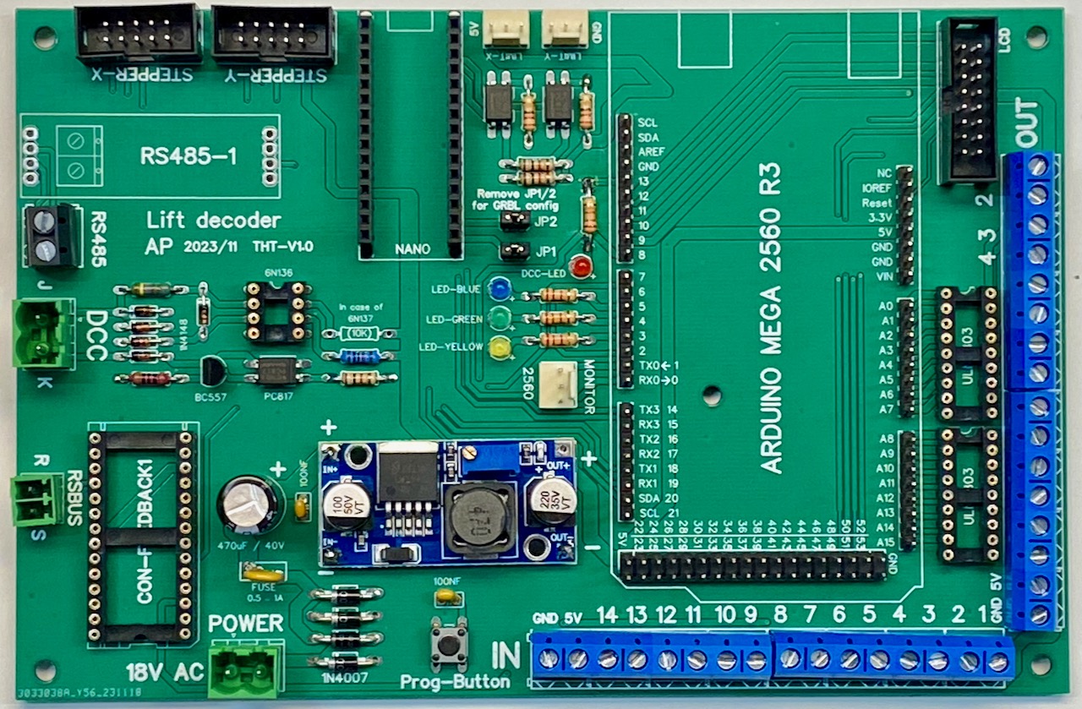
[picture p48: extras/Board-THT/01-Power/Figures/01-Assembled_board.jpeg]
The goal of this step is to set the output of the step-down converter to 5 Volt. We do that *before* we connect the Arduino boards and RS485 module. 

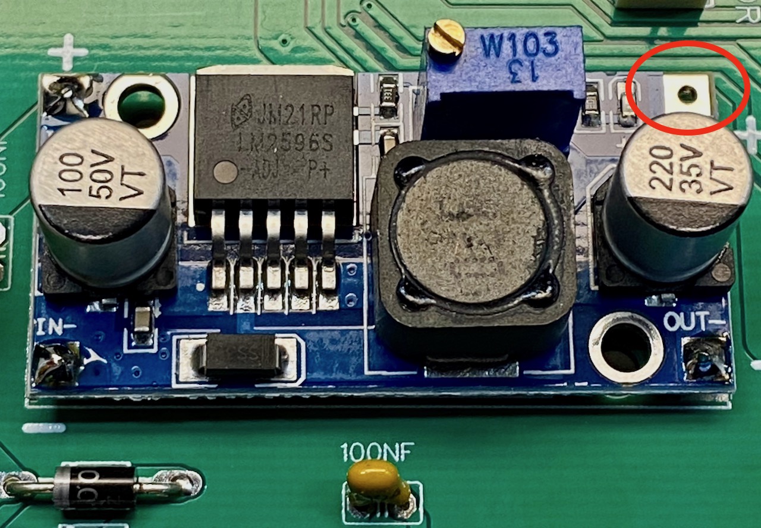
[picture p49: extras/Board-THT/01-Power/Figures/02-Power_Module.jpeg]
To be safe, do not yet solder the **+5V OUT** yet to the remainder of the board. 

Next connect a power supply to the connector labelled **18V AC Power**. The power supply should deliver anything between 8 and 24V; a DC power supply should also work.

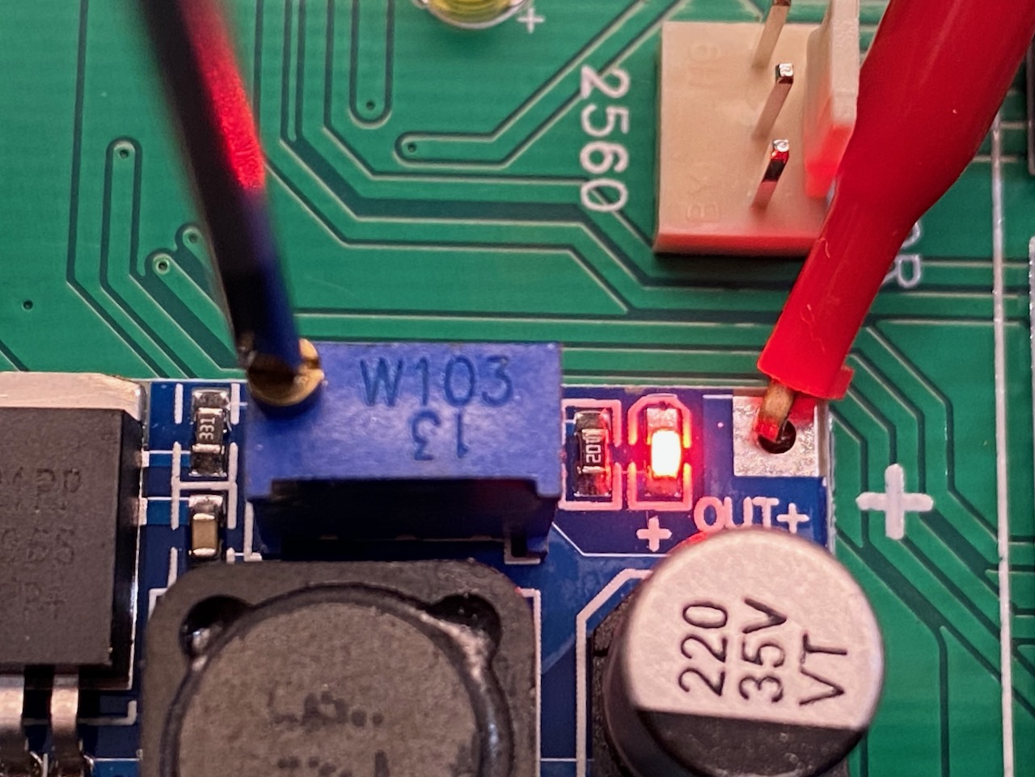
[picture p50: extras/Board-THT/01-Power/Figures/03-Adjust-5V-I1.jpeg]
Next you must set the power to 5V. Connect a voltmeter to GND and the **+5V OUT**. 

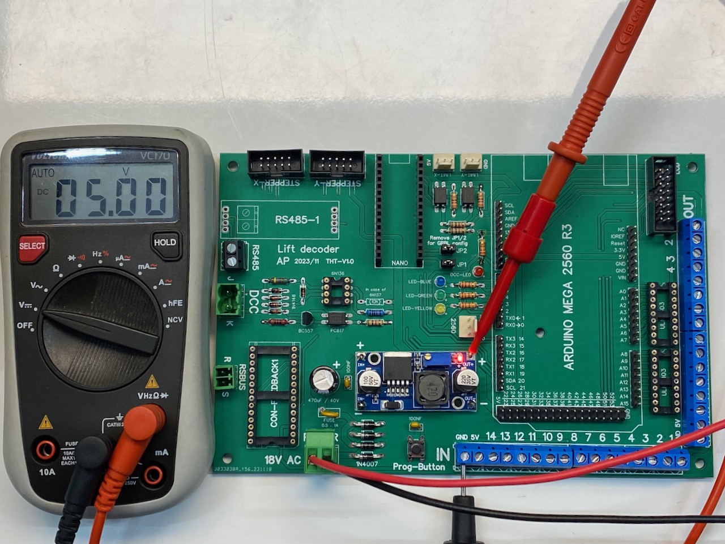
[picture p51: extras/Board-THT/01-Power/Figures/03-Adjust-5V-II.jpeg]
Turn the screw on the potentiometer until the output power is exactly 5 Volt.  

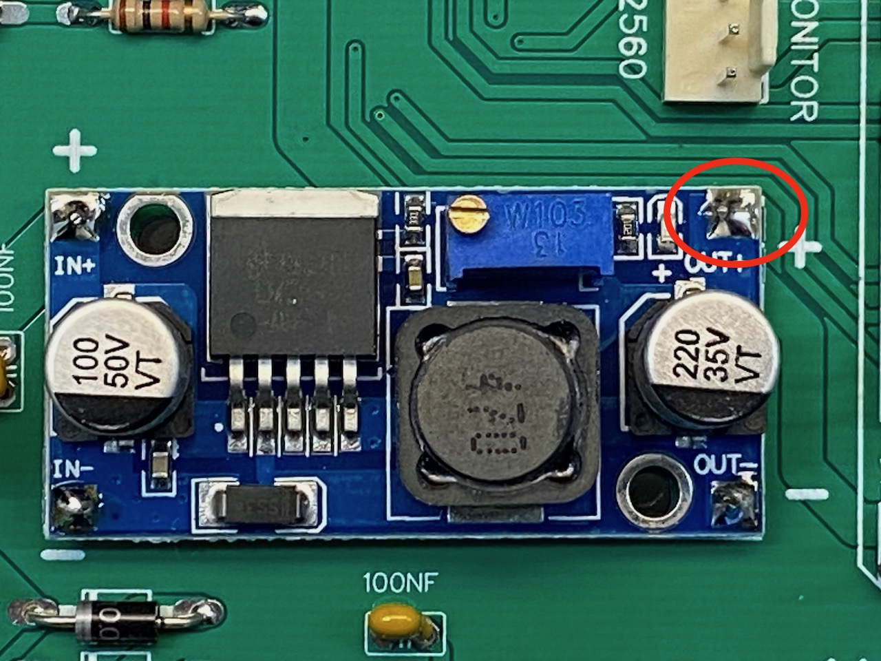
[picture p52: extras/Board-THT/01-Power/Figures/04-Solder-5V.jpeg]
Finally solder the **+5V OUT** to the remainder of the board. 

The power on any additional board should also be set to 5 Volt.

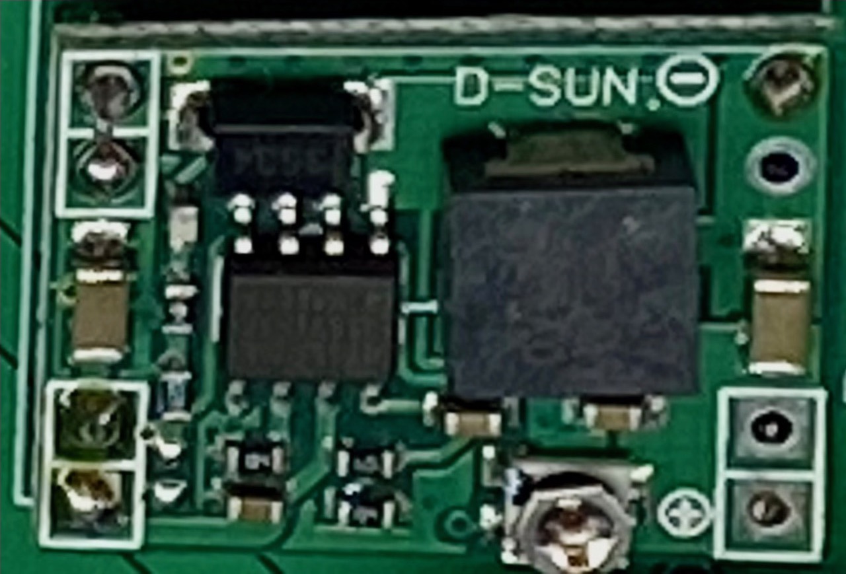
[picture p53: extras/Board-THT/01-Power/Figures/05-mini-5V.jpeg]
The layout of the print also supports 5V mini step-down converters that are based on a 1584 IC, such as shown below.

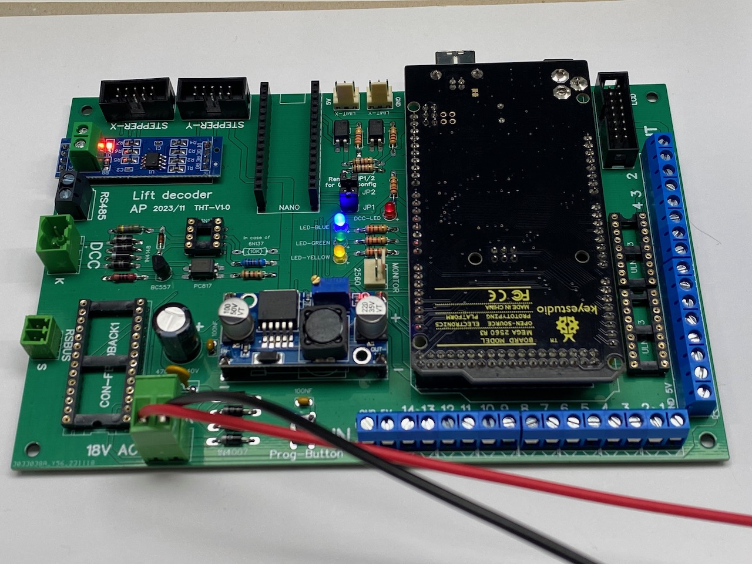
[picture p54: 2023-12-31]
extras/Board-THT/03-Install-and-test-Libraries/Figures/Blink.jpeg

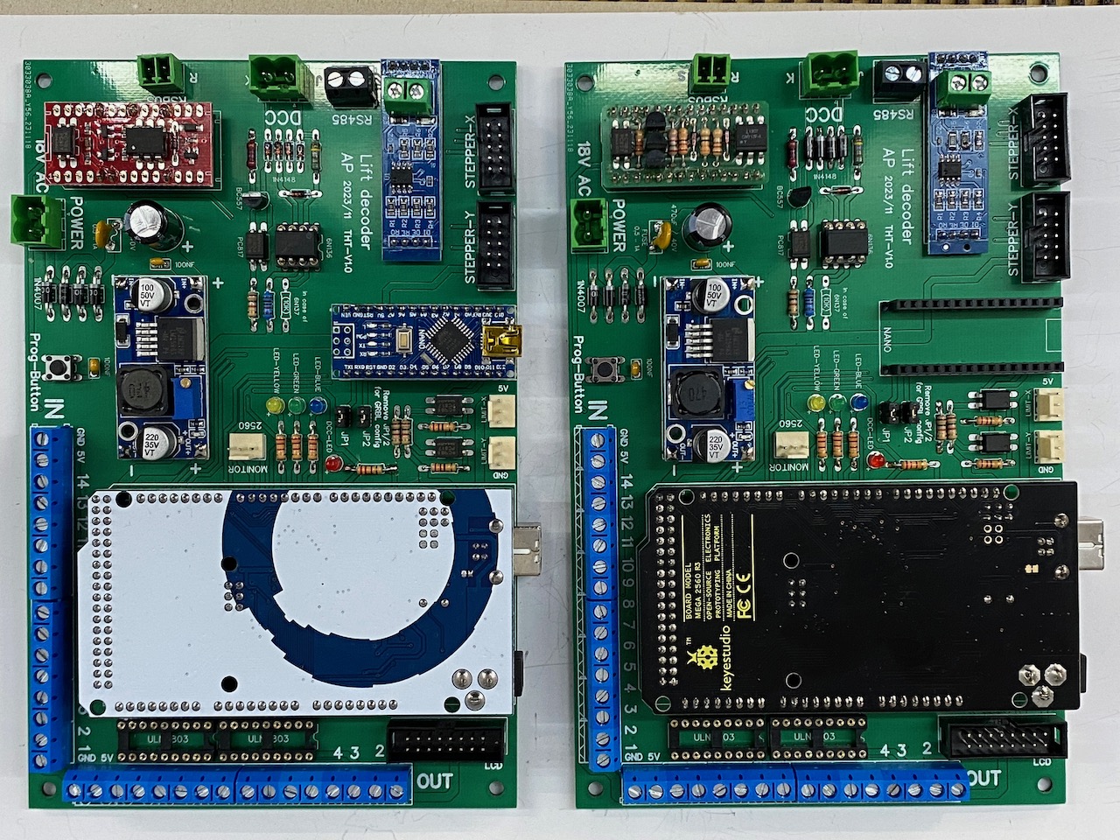
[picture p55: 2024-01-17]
extras/Pictures/THT-Board-assembled-2.jpeg

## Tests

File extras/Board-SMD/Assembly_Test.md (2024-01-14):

## Assembly and test (SMD Board) ##

To make it relatively easy to built the Lift Decoder yourself, a number of instructions and test programs have been written. Assembly and tests is best performed in the following steps (click on each step to see detailed instructions):

  1. [Connect power and test if the power (step-down) electronics is working well](01-Power/Step01-Power.md)
  2. Within the Arduino IDE, install the MegaCore board. [Test compilation and upload of a simple sketch](02-MegaCore-Compilation/Step02-MegaCore-Compilation.md)
  3. Within the Arduino IDE, [install and test the various libraries that are needed](03-Install-and-test-Libraries/Step03-Install-and-test-Libraries.md)
  4. Connect the stepper motors, [configure GRBL and test homing](04-GRBL-and-steppers/Step04-GRBL-and-steppers.md)
  5. [Test if (RS485) communication between the boards is working](05-RS485/Step05-RS485.md)
  6. Optional: [Test if the DCC interface is working](06-DCC/Step06-DCC.md)
  7. Optional: [Test if the RS-Bus interface is working](07-RSBus/Step07-RSBus.md)
  8. Optional: [Install and test the button controller](../../Lift_Buttons/README.md)
  9. Optional: [Install and test the IR-Sensor controller](../../Lift_IR/README.md)
  10. [Install and test the main lift controller](../../Lift_Main/README.md)

SMD Board

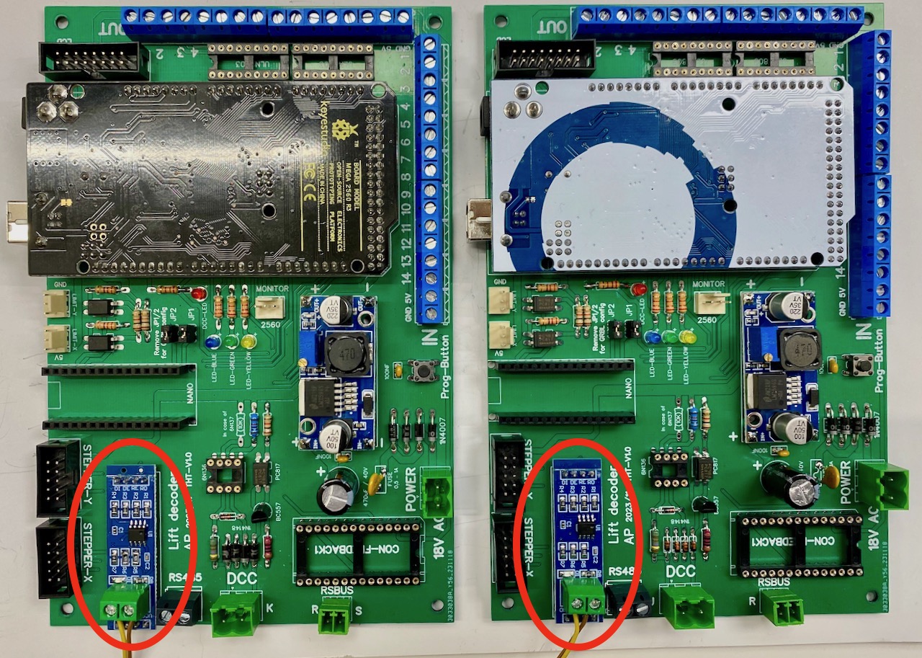
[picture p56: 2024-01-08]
extras/Board-THT/05-RS485/Figures/Test-RS485.jpeg

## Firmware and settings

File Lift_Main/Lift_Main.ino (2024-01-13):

//*****************************************************************************************************
// File:      Lift-Main.ino
// Author:    Aiko Pras
// History:   2021/04/24 AP Version 1.0: RS485 and stepper part ready
//            2022/01/04 AP Version 1.1: DCC part added
//            2024/01/10 AP Version 1.2: mySettings.h added, to ease user customization
//            2024/01/12 AP Version 2.0: Feedback is also provided via the onboard connectors
//
//
// Buttons:
// ========
// If the lift is not moving, the following button behavior is possible:
// - Short press of one of the 0..10 buttons: Lift starts moving to level 0..10
// - Short press of the RESET button: a homing cycle will be initiated
// - Press of ^ or v buttons: Lift moves in small steps up or down (jogging)
// - Long press of one of the 0..10 buttons: position will be stored as new position for that level
//
// While the lift moves, the associated button Led will slowly flash. 
// After the move is complete, the button Led will shortly light and subsequently dimm.
// If a new position is being stored, the button LED will flash quickly
//
// If the lift is moving, we keep polling the button controller, but ignore all buttons except the RESET.
// If the RESET is pushed (short press), the lift will immediately be stopped (see emergence stop below).
//
// DCC address
// ===========
// The common approach for all my DCC decoder boards, is to compile the DCC address with an
// "illegal" value. This triggers the board to notify the user, via blinking of the red LED, that
// a DCC address needs to be entered. Like all other decoder boards, this DCC address can be set using
// the onboard programming button. This new address is permanently stored (in EEPROM), and the next time
// the decoder starts, the valid DCC address is read from EEPROM and the red LED no longer blinks.
// You might prefer to set the DCC address already at compile time, however. This can be done by  
// changing the CV1 and CV9 settings in the file mySettings.h 
//
// RS-Bus address
// ==============
// The onboard programming button is not only used to set the DCC address, but indirectly also the 
// RS-Bus address. If you select a decoder address < 128 (thus a switch addresses <509), the RS-Bus
// address becomes equal to the decoder address (+1). If you select a decoder address >=128, the 
// RS-Bus address becomes 0, meaning "not used". 
// Via the onboard programming button it is therefore not possible to use decoder addresses >=128, 
// in combination with RS-Bus feedback.
// Fortunately, we can still use DCC decoder addresses >=128, in combination with RS-Bus feedback, 
// provided we select these addresses before compilation, in the file mySettings.h.
// We use 12 feedback bits to inform traincontroller (or whatever software we have) at which level
// the lift currently is (0..11). Additional feedback bits are used to signal that the stepper 
// motors are IDLE (the lift has arrived at the requested level) and that no obstacles are detected
// by the IR system. We therefore use 2 RS-Bus addresses. 
//
// Emergency stop
// ==============
// If the lift is moving, it can be stopped by either pushing the RESET button, or by sending a DCC 
// Emergency Stop command (= Broadcast ResetCmd). In both cases the RESET button will quickly flash.
// 1) BUTTON: The Button generates a soft_reset, which immediately halts the steppers and resets Grbl. 
// If reset while in motion, Grbl will throw an Alarm to indicate position may be lost from the 
// motion halt. The Alarm state is signaled via the RESET Button LED, which quickly flashes.
// A second push of the RESET button is needed to leave the Alarm state. The lift stays at an 
// undefined position.
// 2) DCC Emergency Stop command: generates a GRBL feedhold.
//
// Onboard LEDS:
// ============
// LED_GREEN: Power connected / IR sensors are free (or disabled)
// LED_BLUE: Lights if the steppers are busy
// LED_YELLOW: Mimics the LEDs on the remote button panel (without flashing)
// LED_RED: The standard programming and RS-Bus Feedback LED
//
// Adjusting behaviour
// ===================
// Some aspects of the lift decoder's behaviour can be modified by the user of this software.
// See the file mySettings.h for details
//
// Feedback
// ========
// Feedback is provided regarding the lift's position and status. There are three status bits:
// - The IR-sensors are free (provided IR-sensors are active)
// - The Lift has arrived / is at level x. There is no movement and the stepper motors are idle
// - The lift is ready. 
//   If the IR-Sensors are active, this bit is the same as 'IR-sensors are free' AND 'Lift is at level x'.
//   If the IR-Sensors are inactive, this bit is the same as 'Lift is at level x'.
//   Analysing this single bit may, in Train Control software, be easier than two bits.
// During movement of the lift, all feedback bits are cleared.
// Feedback is provided in two ways.
// 1) Using the RS-Bus. We use two addresses; the meaning of the individual bits, is as follows:
//   - Base address    : Level 0..7                (low and high nibble. Bit 0..7)
//   - Base address + 1: Level 8..11               (low nibble.          Bit 0..3)
//   - Base address + 1: IR-sensors are free       (high nibble          Bit 4)
//   - Base address + 1: Lift is at level x        (high nibble          Bit 5)
//   - Base address + 1: Lift Ready                (high nibble          Bit 7)
// 2) Using the connectors on the Main Lift Board connectors (added in V2.0).
// Its purpose is to facilitate the use of alternative feedback systems (such as S88). 
//   - The connectors labelled "IN 1..12" are used to tell which level the lift currently is.
//     The connector labelled "1" is for level "0", etc. 
//   - The connector labelled "IN 13" is used to tell that IR-sensors are free.
//   - The connector labelled "IN 14" is used to tell that lift has arrived / is at level x.
//   - The pin labelled "OUT 1" is to tell that the lift is ready. 
// Note that the IN connectors are directly connected to pins on the ATMega 2560 processor,
// (accidental) shortcut of these pins will destroy the processor. 
// Therefore ensure you always use resistors with a value of 1 kOhm or higher.
//
// Relays
// ======
// As an extra safety measure, it is possible to connect two bi-stable relays to the lift decoder.
// This allows the power of the lift tracks, or the track towards the lift, to be switched off.
// In case the lift is IDLE and at level 0, both relays are swiched to "position 1".
// In all other cases both relays will be swiched to "position 2".
//
//
//*****************************************************************************************************
#include <LiquidCrystal.h>        // Allow LCD output of the current state and position
#include "mySettings.h"           // Allows user of this sketch to tailor the behaviour 
#include "hardware.h"             // Pins for LEDs, DCC input, RS-Bus output etc.
#include "support.h"              // For the LCD Display and some on-board LEDs
#include "rs485.h"                // Use RS485 to read IR-sensors. button status, set button LEDs 
#include "stepper.h"              // Communication with the stepper motor controller (GRBL)
#include "feedback.h"             // Feedback (RS-Bus) specific code
#include "relays.h"               // For connecting two external relays 


//*****************************************************************************************************
// SETUP
//*****************************************************************************************************
unsigned int firstDecoderAddress;

void mySettings() {
  #if defined(NO_HOMING) 
    cvValues.write(StartHoming, 0);              // CV-defaults = 1
  #endif
  #if defined(NO_IR_SENSORS) 
    cvValues.write(IR_Detect, 0);                // CV-defaults = 1
  #endif
  #if defined(ENABLE_LCD)            
    cvValues.write(LCD_Display, 1);              // CV-defaults = 1
  #endif
  #if defined(SERIAL_MONITOR)
    cvValues.write(Serial_Line, SERIAL_MONITOR); // Default value = 0
  #endif
  #if defined(CV1)
    cvValues.write(myAddrL, CV1);                // Default value = 0x01
  #endif
  #if defined(CV9)
    cvValues.write(myAddrH, CV9);                // Default value = 0x80
  #endif
  #if defined(RS_ADDRESS)
    cvValues.write(myRSAddr, RS_ADDRESS);        // Default value = 0
  #endif
}


void setup() {
  // The monitor is connected via Serial (UART0) and the GRBL controller via Serial2 (UART2)
  // The Serial_Line CV disables (value = 0) or enables the Serial interface.
  // This interface is connected to UART0, provides 5V logic and may be connected to a computer via a
  // Serial to USB converter. 
  // If enabled, interference on the interface line may be possible. Enabling is needed, however, to
  // make GRBL configuration changes (for example, $27=8.6 to change the zero offset).
  // A value of 1 gives basic (debugging) information, a value of 2 gives detailed information.
  if (cvValues.read(Serial_Line)) Serial.begin(115200);
  Serial2.begin(115200);                  // GRBL = MEGA 328 
  // While debugging, the lcd_display may be active for debugging
  lcd_display.init();
  // Initialise the DCC and RS-Bus part of the lift decoder. See above for details regarding addresses.
  // After cvValues.init() is called, CV default values may be modified using cvValues.defaults[...]
  cvValues.init(LiftDecoder,12);          // software version may be added as 2nd parameter. Default: 10  
  mySettings();                           // To override default settings with values from mySettings.h
  decoderHardware.init();                 // Use the CV values stored in EEPROM
  // The softare supports a maximum of 12 lift levels; each level has its own switch address.
  // For 12 switch addresses, we need to listen to 3 decoder addresses
  firstDecoderAddress = cvValues.storedAddress();
  accCmd.setMyAddress(firstDecoderAddress, firstDecoderAddress + 2);
  // Initialise the feedback system. At start-up, the values for lift.level and lift.currentPosition 
  // are zero. The level bit and STEPPER_IDLE bit will be set. The RS-Bus master will be informed.
  feedback.init(cvValues.read(myRSAddr));
  // To ensure a consistent state, do a homing cycle first. Wait 1 sec to ensure GRBL is up and running
  delay(1000);
  if (cvValues.read(StartHoming)) reset_object.home(); 
  // Display some settings
  if (cvValues.read(Serial_Line)) {
    #ifdef BOARD_SMD
      Serial.println("SMD board"); 
      #endif
    #ifdef BOARD_THT
      Serial.println("THT board"); 
      #endif
    Serial.print("myAddrL: "); 
    Serial.println(cvValues.read(myAddrL)); 
    Serial.print("myAddrH: "); 
    Serial.println(cvValues.read(myAddrH)); 
    Serial.print("First DCC decoder address:"); 
    Serial.println(firstDecoderAddress);   
    Serial.print("First RS-Bus address:"); 
    Serial.println(cvValues.read(myRSAddr)); 
    Serial.print("IR-sensors: ");
    Serial.println(cvValues.read(IR_Detect));
    Serial.println(); 
  }
}




void serialMonitor() {
  // For testing purposes read from monitor port and send to GRBL port. Note that we can't read here 
  // what comes back from the GRBL controller, since that is handled by the grbl parser.
  // We have installed GRBL V1.1h (with modified config.h)
  // - $$  = view settings
  // - x20 = Move X stepper to 20 mm
  // - ?   = status request
  if (cvValues.read(Serial_Line)) {
    if (Serial.available()) {
      char inByte = Serial.read();
      Serial2.print(inByte);
    }
  }
}


//*****************************************************************************************************
// Main Loop
//*****************************************************************************************************
uint8_t level;
bool dccReset = 0; 

void loop() {
  // The main loop handles parses status and receices commands from:
  // - The serial monitor 
  // - The Stepper controller
  // - The IR-Led controller
  // - The Button controller
  // - The DCC controller
  // The serial monitor, Button and DCC controller issue commands to move the steppers 
  // Feedback information is provided via the RS-Bus, LCD display and Button LEDs. 
  
  //===================================================================================
  // Step 1: Serial monitor
  // For testing purposes we accept input via the serial monitor. Input should be valid 
  // GRBL commands, such as G90 X20 Y20 (absolute position) or G91 X20 Y20 (delta move)
  serialMonitor();
  
  //===================================================================================
  // Step 2: Stepper Controller 
  // Update the stepper controller. This involves parsing characters received via the
  // serial interface from the GRBL controller, interpreting the received GRBL response
  // message and periodically sending the GRBL controller a poll message (?).
  // Via the stepper controller we also update the jog_object, which handles stepper 
  // moves while an UP or DOWN button is being pressed.
  stepper.update(); 
  //
  // After parsing a number of GRBL response characters we may conclude that
  // the stepper state and/or stepper position have changed
  if (stepper.state_changed()) {
    lcd_display.show();     // Show the buttonnumber and the stepper status
    if (stepper.state == grbl::IDLE) {
      digitalWrite(LED_BLUE, LOW);          // Indicate the steppers are idle
      btn_cntrl.prepare_LED(LED_OFF, btn_cntrl.buttonNumber);  // buttonNumber: 0..13
      // Ensure that the lift position (in mm) matches the requested level.
      // In the (unlikely) case that only one of the two ATMega processors (2560 and 328)
      // performed a reset, both processors will be in different and thus inconsistent
      // states. If that happens, the user should perform a homing cycle (push RESET)
      if (strcmp(lift.currentPosition,lift.positions[lift.level]) == 0) {
        feedback.setLiftLevel(lift.level);
        relaysCntrl.lift_idle(lift.level);  // if at level 0, switch the relays to POS1
        if (cvValues.read(Serial_Line)) {
          Serial.print("Lift at level: ");
          Serial.println(lift.currentPosition);
        }
      }      
      else {
        feedback.clearFeedbackBits();       // to catch fast changes, such as step-up
        digitalWrite(LED_BLUE, HIGH);       // Indicate the steppers are busy 
      }
    }
    else {
      feedback.clearFeedbackBits();         // to catch normal changes
      digitalWrite(LED_BLUE, HIGH);         // Indicate the steppers are busy 
    }
  }
  else if (stepper.position_changed()) { 
    lcd_display.show();
    relaysCntrl.lift_moving();              // Not at level 0, switch the relays to POS2
  }
  //===================================================================================
  // Step 3: Send the IR-Sensor controller a poll message, and to the Button controller
  // a poll message or a command to change the button LEDs.
  // The controller object send these messages over the RS-485 bus with 50ms intervals.
  controllers.talk485();
  // 
  //===================================================================================
  // Step 4: If the IR-Sensor controller changes state, send feedback via the RS-Bus
  // sensorIsFree is a boolean variable, indicating if no IR-lightbeam is blocked
  if (ir_cntrl.stateChanged()) {
    feedback.irFree = ir_cntrl.sensorIsFree;
    feedback.sendMainNibble();
  }
  //
  //===================================================================================
  // Step 5: Button controller
  // Did an event occur associated with a level button (buttons 0..10)
  // and is this not the button of the level we already are?  
  if (btn_cntrl.level_button_event()) {
    if (stepper.state == grbl::IDLE) {
      // Store the button number, to enable future display and LED-OFF messages  
      lift.level = btn_cntrl.buttonNumber;
      // If the stepper motors are not moving, new commands can be accepted 
      if (btn_cntrl.buttonAction == PRESSED) {
        // Immediately after being pressed, put the associated LED on
        btn_cntrl.prepare_LED(LED_ON, lift.level);
      }
      else if (btn_cntrl.buttonAction == SHORTPRESS) {
        // In case of a short press, the lift moves to the requested level
        // provided the lift's position is not yet at the requested level
        if (strcmp(lift.currentPosition,lift.positions[lift.level])) {
          lift.move(lift.level);
          lcd_display.show();
          btn_cntrl.prepare_LED(FLASH_SLOW, lift.level);
        }
        else btn_cntrl.prepare_LED(LED_OFF, lift.level);
      }
      else if (btn_cntrl.buttonAction == LONGPRESS) {
        // The current position should be used and stored
        strcpy(lift.positions[lift.level], lift.currentPosition);
        lift.storePosition(lift.level);
        btn_cntrl.prepare_LED(LED_OFF, lift.level);
      }
    }
  } 
  // Did an event occur associated with the UP or DOWN button?
  if (btn_cntrl.up_down_button_event()) {
    if (stepper.state == grbl::IDLE) {
      // If the stepper motors are not moving, new commands can be accepted        
      if (btn_cntrl.buttonAction == PRESSED) {
        // Immediately after being pressed, start moving and put the associated LED on
        if (btn_cntrl.buttonUpOrDown == btn_cntrl.UP) jog_object.start(jog_object.UP);
        else jog_object.start(jog_object.DOWN);
        btn_cntrl.prepare_LED(LED_ON, btn_cntrl.buttonNumber);
      }
    }
    if (btn_cntrl.buttonAction == RELEASED) {
      jog_object.cancel();
      btn_cntrl.prepare_LED(LED_OFF, btn_cntrl.buttonNumber); // switch off the LED for this button
    }
  }  
  // Did an event occur associated with the RESET button?
  // If we the state is IDLE, a homing cycle will be started
  // If the state is RUN, JOG or HOLD, a Soft-Reset message will be send
  // If the state is ALARM, an unlock message will be send  
  // If the alarm state is unlocked, a new Homing cycle may be needed 
  if (btn_cntrl.alarm_button_event()) {
   if (btn_cntrl.buttonAction == PRESSED) {
     switch (stepper.state) {
       case grbl::IDLE:
         feedback.clearFeedbackBits();      // We leave the IDLE state and the current level
         lift.level = 0;                    // This will become the new level
         btn_cntrl.prepare_LED(FLASH_SLOW, RESET_BUTTON);
         lcd_display.homing();
         reset_object.home(); 
       break;
       case grbl::RUN: 
       case grbl::JOG: 
       case grbl::HOLD: 
         reset_object.soft_reset(); 
         btn_cntrl.prepare_LED(FLASH_FAST, RESET_BUTTON);
       break;
       case grbl::ALARM: 
         reset_object.unlock(); 
         btn_cntrl.prepare_LED(LED_OFF, lift.level);
       break;
       default:                             // UNKNOWN, HOMING
       break;
      }
    }
  }

  //===================================================================================
  // Step 6: DCC controller
  // If the DCC Controller receives an emergency stop, the best seems to send a  
  // feed-hold command. This allows to lift to continue its movement afterwards. 
  // In case the lift should not restart its movement after a DCC emergency stop, while still  
  // in the HOLD state the reset-button may be pushed and a soft-reset will be performed
  if (dcc.input()) {
    switch (dcc.cmdType) {
      // The next two to stop the lift via feedhold
      // ResetCmd is send after the STOP button on the LH100 is pushed, or after TC Einfrieren
      // MyEmergencyStopCmd is never received from a LZV100, but included for possible future versions
      case Dcc::ResetCmd :
      case Dcc::MyEmergencyStopCmd:  
        reset_object.feedhold(); 
        btn_cntrl.prepare_LED(FLASH_FAST, RESET_BUTTON);
        lcd_display.show();
        dccReset = true;
      break;
      // Emergency stop is over. Send a resume
      case Dcc::SomeLocoSpeedFlag :
      if (dccReset) {
        reset_object.resume();
        btn_cntrl.prepare_LED(LED_OFF, RESET_BUTTON);
        dccReset = false;
        lcd_display.show();
      }
      break;
      // Move the lift to the requested leve;
      case Dcc::MyAccessoryCmd :
        if (accCmd.command == Accessory::basic)
        // If the stepper motors are inactive and the switch poition is '+', move the lift
        if ((stepper.state == grbl::IDLE) && (accCmd.position == 1)) {
          lift.level = (accCmd.decoderAddress - firstDecoderAddress) * 4 + accCmd.turnout - 1;
          lift.move(lift.level);
          if (cvValues.read(Serial_Line)) {
            Serial.print("Move lift to level: ");
            Serial.println(lift.level);
          };
          lcd_display.show();
        }
      break;      
      case Dcc::MyPomCmd :
        cvProgramming.processMessage(Dcc::MyPomCmd);
        break;
      case Dcc::SmCmd :
        cvProgramming.processMessage(Dcc::SmCmd);
        break;
      default:
        break;
    }
  }
  // As frequent as possible we should call the RS-Bus address polling routine, check if the 
  // programming button is pushed, and if the status of the onboard LED should be changed.
  decoderHardware.update();
  feedback.update();
  relaysCntrl.update();
}

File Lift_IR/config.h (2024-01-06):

//******************************************************************************************************
//
// file:      config.h
// author:    Aiko Pras
// history:   2024-01-6 V1.0.0 ap initial version
//
// purpose:   Variables and #defines that must be set by the user
//
//******************************************************************************************************
#pragma once


// 1) Tell the sketch which board we are using
// ===========================================
// All lift controller code has been developed for the Arduino 2560 microcontroller.  
// It is intended for the Lift decoder boards that are available from the OSHWLAB.
// - SMD board: https://oshwlab.com/aikopras/support-lift-controller
// - THT board: https://oshwlab.com/aikopras/lift-decoder-arduino-mega-tht
// Select the board that will be used. 
#define BOARD SMD
// #define BOARD THT


// 2) Tell the sketch which I/O ports are used for sensors
// =======================================================
// The following #define tells which Inputs and Outputs of the Liftdecoder board are being used.
// Modify to represent your specific sensor setting
// The lowest order bit corresponds to the IN/OUT pair of the blue connectors that are labelled 1
// Examples:
// - 0b0000000000000001 a single sensor is connected to IN/OUT 1
// - 0b0000000000000011 two sensors are connected to IN/OUT 1 and 2
// - 0b0000000000000010 a single sensor is connected to IN/OUT 2
// - 0b0000111111111111 twelve sensors are connected to IN/OUT 1..12
// - 0b0011111111111111 all 14 sensors are connected
#define MASK_SENSORS_CONNECTED 0b0000111111111111


// 3) Set the sensor sensitivity
// =============================
// The sensitivity of the IR Leds and sensors is best around 38kHz. 
// Therefore most IR systems operate at 38 Khz. At that frequency, a full pulse takes 26,3 us
//
//          +-------+
//          |       |
//          |       |
//          +       +-------+
//            13 us   13 us                                
//
// Unfortunately, at 38Khz the system may become too sensitive, and suffer from indirect reflections.
// Reflections result in false negatives: although a train blocks the direct IR-beam, this is not detected.
//
// Fortunately the LED and sensor also operate at lower (or higher) frequencies, although less sensitive.
// To decrease the sensitivity of the sensors, we will lower the frequency (in kHZ).
// In practice a value of 25Khz seems to give good results, but you may experiment with this value
// by modifying the #define KHZ value.
//
// To avoid the sensor from saturation, the burst of IR pulses may not become too long. 
// Reasonable values are 15 to 30 pulses, which corresponds (roughly) to 375 us (15*25) till 750us.
#define KHZ 25                       // Frequency at which we operate the IR system
#define BURST_TIME 600               // Time in us the burst will last


// 4) Set the RS-Bus addresses
// ===========================
// Although the Main Lift Controller board signals to the DCC system / control computer if all IR-Sensors
// are free or not (single bit), it may be convenient to also know the status of each individual sensor.
// This is particularly useful to detect possible errors. 
// Therefore we also use the RSBus to send feedback regarding individual sensors
// We use two RSBus feedback addresses, to accommodate a maximum of 16 sensors (although the board 
// supports "only" 14 sensors). You may change the addresses to whatever you like.
// If you don't use RSBus feedback, just keep the values below to avoid compile errors.
const uint8_t RS_AddresLow = 124;     // 1.. 128
const uint8_t RS_AddresHigh = 125;    // 1.. 128


// 5) Increase speed
// =================
// To increase speed, we can use two of the three GPIORs that are available on a ATMega 2560. 
// This requires, however, that these GPIORs are not yet used elsewhere. 
// The AP-DCC-Library, for example, already uses GPIOR0 and GPIOR1.
// In case we also need the AP-DCC-Library, use the volatile uint8_t variables instead
#define PORT GPIOR0                   // Fast, but may interfere with other libraries
#define BITMASK GPIOR1                 
//volatile uint8_t PORT;              // Slow, but more portable
//volatile uint8_t BITMASK;

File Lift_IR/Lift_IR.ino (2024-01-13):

// ***********************************************************************************************************
// 
// purpose:   Control of the Loklift IR sensors
// File:      Lift_IR.ino
// Author:    Aiko Pras
// History:   2022/01/25 AP Version 1.0
//            2024/01/06 AP Version 2.0 - Added RSBus feedback, debugging via the Serial interface and LEDs.
//                                        Before compilation, make sure you've set the variables and #defines
//                                        contained in the file mySettings
// 
// The code is has been tested on the following lift controller boards 
// - SMD board: https://oshwlab.com/aikopras/support-lift-controller
// - THT board: https://oshwlab.com/aikopras/lift-decoder-arduino-mega-tht
//
// Instructions for compiling, see
// - SMD board: https://github.com/aikopras/Lift_Vitrine/blob/main/extras/Board-SMD/Compile.md
// - THT board: https://github.com/aikopras/Lift_Vitrine/blob/main/extras/Board-THT/Compile.md
//
// LEDs:
// - Blue:Indicates reception of RS485 message from the main decoder board  Should blinks 10x per second.
// - Green: Indicates if the IR-Sensors are free (no train blocks the IR-beam). On = free
// - Yellow: Decoder is in debugging mode
// - Red: Blinks whenever a RSbus feedback message is send. Also twice at startup.
//
// Button: if pushed, debugging mode is turned on/off. 
// In debugging mde, status information of each individual sensor will be send over the Serial Monitor. 
//
// ***********************************************************************************************************
//                                           Do not edit below this line
// ***********************************************************************************************************
#include <AP_DCC_Decoder_Core.h>      // Library for a basic DCC accesory decoder with RS-Bus feedback
#include <AP_RS485_Lift.h>            // Library to communicate with the main lift decoder
#include "mySettings.h" 
#include "hardware.h" 
#include "IR-Sensor.h"

RS485_Lift myRS485(IR_LEDS_ADDR);    // Instantiate the myRS485 object

IR_Sensors irSensors;                // Instantiate the irSensors object
uint16_t sensorValuesNew = 0;        // Set every 100ms by IR_Sensors::feedbackBit
uint16_t sensorValues = 0;           // Old values

DccLed redLed;                       // LED that signals transmission of RSBus messages
DccButton button;                    // Push to enter debug mode (use Serial interface for sensor feedback) 
bool debugFlag;                      // Determines if we are in debug mode or not

extern RSbusHardware rsbusHardware;  // This object is defined and instantiated in the RSbus library
RSbusConnection rsbusFirst;          // Object that represents the sensors 1..8
RSbusConnection rsbusSecond;         // Object that represents the sensors 9..16
unsigned long TLast;                 // Support variable for RSBus transmission


// ***********************************************************************************************************
void setup() {
  // The green LED indicates that all sensors are free 
  pinMode(LED_GREEN, OUTPUT);
  digitalWrite(LED_GREEN, HIGH);
  // The blue LED indicates RS485 bus activity
  pinMode(LED_BLUE, OUTPUT);
  digitalWrite(LED_BLUE, LOW);
  // The yellow LED indicates debugging mode (status info is send via the Serial Interface)
  pinMode(LED_YELLOW, OUTPUT);
  digitalWrite(LED_YELLOW, LOW);
  //
  // The timers (4 and 5) are used to create the IR beam
  irSensors.init_timers();
  //
  // RSbus specific initialisation
  rsbusHardware.attach(rsBusUsart, rsBusRX);
  rsbusFirst.address = RS_AddresLow;
  rsbusSecond.address = RS_AddresHigh;
  redLed.attach(ledPin);
  TLast = millis();
  //
  // Debugmode specific initialisation
  button.attach(buttonPin);
  delay(500);                 // some time to allow the hardware to initialise
  button.read();              // Initial read is needed, to start in normal (not debug) mode 
  debugFlag = 0;
  //
  redLed.start_up();          // Blink twice to indicate startup
}


// *** RSBus ***
void PrepareRSBusFeedback() {
  // Stores in a buffer RSBus feedback messages for sensor values that have been changed
  if (rsbusHardware.rsSignalIsOK) {
    if ((sensorValues & 0x000F) != (sensorValuesNew & 0x000F)) rsbusFirst.send4bits(LowBits,    sensorValuesNew & 0x000F);
    if ((sensorValues & 0x00F0) != (sensorValuesNew & 0x00F0)) rsbusFirst.send4bits(HighBits,  (sensorValuesNew & 0x00F0) >> 4);
    if ((sensorValues & 0x0F00) != (sensorValuesNew & 0x0F00)) rsbusSecond.send4bits(LowBits,  (sensorValuesNew & 0x0F00) >> 8);
    if ((sensorValues & 0xF000) != (sensorValuesNew & 0xF000)) rsbusSecond.send4bits(HighBits, (sensorValuesNew & 0xF000) >> 12);
    if (sensorValues != sensorValuesNew) redLed.feedback();
  }
}


void SendRSBusFeedback() {
  // Listen to RS-Bus polling messages for our turn
  rsbusHardware.checkPolling();
  // The RSBus can not send faster than once per 30 ms. Therefore we check only once per 20ms
  unsigned long TNow = millis();            // millis() is expensive, so call it only once
  if ((TNow - TLast) >= 20) {               // 20ms passed?
    TLast = TNow; 
    // If a RS-Bus feedback decoder starts, or after certain errors, it needs to send its feedback data to the master station
    if (rsbusFirst.feedbackRequested)  rsbusFirst.send8bits(0);
    if (rsbusSecond.feedbackRequested) rsbusSecond.send8bits(0);
    // Check if the RSBus buffer contains feedback messages, and give these to the ISR and USART for actual transmission
    rsbusFirst.checkConnection();
    rsbusSecond.checkConnection();
  }
}


// *** LEDs ***
void setLed(byte nummer) { digitalWrite(nummer, HIGH); }
void clearLed(byte nummer) { digitalWrite(nummer, LOW); }
void toggleLed(byte nummer) { digitalWrite(nummer, !digitalRead(nummer)); }
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

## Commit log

2023-01-22 Small error corrected
    A test was forgotten that caused a "flood of RS-Bus messages" as soon as the IR-Sensors detected a busy situation
    [Lift_Main.ino, rs485.cpp]
2023-11-01 Test Program for GRBL-Serial communication for Lift decoder board
    Test program to easily test GRBL, using the Serial connector on the Lift decoder board
2023-11-02 Test sketches added
    Two sketches were added to check the serial communication between the Lift decoder board / Arduino Mega and the UNO/Nano board running GRBL
2024-01-06 IR-Sensor software updated to V2
    Software for the IR-Sensors is updated. Additions include RS-Bus feedback, the addition of a debug mode, modified behavior of LEDs and localization of all user modifyable settings in a single file ca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
2024-01-08 Description added on how to test GRBL
    The description to compile, upload, configure and test GRBL has been added. The description is available for the SMD as well as THT board.
    [Magnet-1.stl, Magnet-2.stl, Magnet-3.stl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]
2024-01-13 Error in #defines corrected
    There was an error in the Lift_IR #defines analysis
    [hardware.h, mySettings.h]
2024-01-13 V2 of the Lift Decoder
    Major update of the Main Lift Decoder software. Should be easier to customize, runs also on the THT board, feedback system changed to accommodate also other feedback systems
2024-01-13 Lift Buttons updated for THT board
2024-01-14 Version 2
    Major revision of the Software. Also tested on THT board. Extensive compile and test instructions added. Also local feedback possible.
2024-02-13 Update relays.cpp
    Bug corrected that prevented operation of the relays
